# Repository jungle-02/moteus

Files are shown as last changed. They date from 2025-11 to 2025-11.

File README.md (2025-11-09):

# moteus brushless servo #

This contains full designs for the moteus brushless servo actuator,
including firmware and PCBs.

**WARNING**: This is not just a software project.  It includes designs
for moderately high power electronics.  It has not yet burned down my
(or anyone's that I know of) house, but there are no guarantees.

# Specifications #

| Name | r4.11 | c1 | n1 | x1 |
|---|---|---|---|---|
| Voltage Input | 10-44V | 10-51V | 10-54V | 10-54V |
| Peak Electrical Power  | 900W @ 30V | 250W @ 28V | 2kW @ 36V | 1.3kW @ 36V |
| Mass | 14.2g | 8.9g | 14.6g | 23.8g |
| Control Rate | 15-30kHz | - | - | - |
| PWM Switching Rate | 15-60kHz | - | - | - |
| CPU | STM32G4 | - | - | - |
| Uncooled phase current | 12A | 5A | 9A | 25A |
| Cooled phase current | 32A | 14A | 26A | 62A |
| Peak phase current | 100A | 20A | 100A | 120A |
| Communications | 5Mbps CAN-FD | - | - | - |
| Dimensions | 46x53mm | 38x38x9mm  | 46x46x8mm | 56x56x10mm  |

Assembled and tested boards can be purchased at: https://mjbots.com

# Directory structure #

* hw/ - hardware (mechanical and electrical designs)
  * controller/ - PCB design for moteus-r4.11
  * c1/ - PCB design for moteus-c1
  * n1/ - PCB design for moteus-n1
  * x1/ - PCB design for moteus-x1
* fw/ - firmware for brushless controller
* lib/ - client side software
* utils/ - diagnostic tools
* tools/ - bazel build configure
* docs/ - documentation

# Documentation #

* [Quick Start](https://mjbots.github.io/moteus/quick-start)
* [All Documentation](https://mjbots.github.io/moteus/)
* [Discord](https://discord.gg/W4hUpBb)

# Misc #

 * 

# How to support moteus development #

The easiest way to support development the moteus hardware and firmware is as follows:

1) Buy things from https://mjbots.com
2) Build awesome machines!

That's it!  If for some reason you want to go above and beyond, you can sponsor mjbots through github: https://github.com/sponsors/mjbots

# License #

All files contained in this repository, unless otherwise noted, are
available under an Apache 2.0 License:
https://www.apache.org/licenses/LICENSE-2.0

# Trademark #

mjbots Robotic Systems LLC owns and protects the "mjbots" and "moteus" trademarks in many jurisdictions.

If you want to use these names in your project or product, please read the [Trademark Policy](https://mjbots.com/trademark-policy)

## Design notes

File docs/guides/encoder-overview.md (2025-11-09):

# Encoder Overview

This section describes the various ways moteus can be configured to use encoders to sense the rotor, output, or auxiliary devices.  If you intend to only use the onboard on-axis magnetic encoder, you can skip this section.

## Introduction

moteus uses encoders to properly control a motor. Encoders provide the feedback needed to know where the motor is and how fast it's moving. Understanding which encoder(s) to use and how to configure them is one of the key decisions you need to make when designing a system, as for many applications encoder selection is the primary determinant of performance parameters like maximum stiffness, control stability and whether homing will be necessary.

Moteus uses encoders for two distinct purposes. First, it needs **commutation** feedback - the electrical relationship between the motor's stator and rotor to apply torque correctly. Second, it needs **output** feedback - the position and velocity of your output shaft to follow commanded trajectories. A single encoder can serve both purposes, or you can use separate encoders for each.

The good news is that moteus comes with an onboard AS5047P or MA600 magnetic encoder that works out of the box for many applications. This encoder mounts on-axis with the motor. For many use cases, especially those without gear reductions, this is all you need. However, if you're using hall sensors, need higher resolution, or have a gear reducer that you want to measure the output of a reducer or other auxiliary devices, you'll want to add other encoders.

In this guide, we'll cover a few common variants and leave the rest for [the detailed encoder reference](../reference/encoders.md).

## Common Configurations

Here are the most common encoder configurations you'll encounter:

**Default configuration (onboard encoder only):** The AS5047P or MA600 onboard encoder serves as both commutation and output sensor. This works well for many applications, especially those without a reducer installed or with a reducer where either the absolute position of the output is not required or a homing step is permitted.

**Adding hall sensors:** Hall effect sensors provide robust commutation feedback and are useful in high-vibration environments or when cost is a primary concern.  When used as the only encoder, the resulting system will have poor low-velocity and position tracking performance.

**Dual encoder setups:** Using one encoder for commutation (typically the onboard or hall sensors) and a separate high-resolution encoder for output position provides the best performance for precision applications.

These two options are described in separate guides below:

- [Motor with Hall Effects](hall-effects.md) - Adding hall sensors for commutation
- [Dual Encoders](dual-encoders.md) - Using separate encoders for commutation and output

Once again, for detailed information about encoder configuration parameters, see the [Detailed Encoder Reference](../reference/encoders.md).

## Next Steps

Once the encoder has been configured, then you are ready to move on to the [motor calibration procedure](calibration.md).

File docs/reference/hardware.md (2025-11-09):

# Hardware Specifications

## CAD and Models

| Name | 2D CAD | 3D Model |
|---|---|---|
| moteus-c1 |[2D CAD](https://github.com/mjbots/moteus/blob/0.1-20240430/hw/c1/r1.2/20240305-moteus-c1-r1_2.pdf) | [STEP](https://github.com/mjbots/moteus/blob/0.1-20240430/hw/c1/r1.2/20240305-moteus-c1-r1_2.step) |
| moteus-r4 |[2D CAD](https://github.com/mjbots/moteus/blob/main/hw/controller/r4.5/20210124-moteus-controller-r45-mechanical.pdf) | [STEP](https://github.com/mjbots/moteus/blob/main/hw/controller/r4.5/20210124-moteus-controller-r45-mechanical.step) |
| moteus-x1 | [2D CAD](https://drive.google.com/file/d/1R7wuc7vk1khD5ZvDWPy54Bx4PgHYiUCu/view) | [STEP](https://drive.google.com/file/d/19tJa4gzy0ZBWYYsaJA-Du0PgzoDWizjL/view?usp=sharing) |
| moteus-n1 | [2D CAD](https://drive.google.com/file/d/1Ic65vT8BSeTtqz6uqd8C7l68aOMy3bMz/view?usp=share_link) | [STEP](https://drive.google.com/file/d/1wxX5G6kX6M6YZGGSceiXTOUZycxRaSIE/view?usp=share_link) |

## Electrical Limits

| Name | Min Voltage | Nominal | Abs Max Voltage | Peak Output | 3V Aux |  5V Aux | 12V Aux |
|---|---|---|---|---|---|---|---|
| moteus-c1 | 10V | 24V | 51V (<= 12S) | 20A | 50mA | 100mA | N/A |
| moteus-r4 | 10V | 24V | 44V (<= 10S) | 100A | 100mA | N/A | N/A |
| moteus-x1 | 10V | 24V | 54V (<= 12S) | 120A | 100mA | 200mA | 150mA |
| moteus-n1 | 10V | 24V | 54V (<= 12S) | 100A | 100mA | 200mA | N/A |

## Power Limits

The allowable maximum power for each moteus controller depends upon
the input voltage and PWM switching frequency.  The below table gives
the maximum allowable power at `servo.pwm_rate_hz=30000`.

| Name | Peak power | | High input power |
|---|---|---|---|
| moteus-r4  | <= 30V 900W  | linear derated | >= 38V 400W |
| moteus-c1  | <= 28V 250W  | linear derated | >= 41V 150W |
| moteus-n1  | <= 36V 2000W | linear derated | >= 44V 1000W |

For other values of `servo.pwm_rate_hz`, the allowable maximum power
changes linearly with the PWM rate, so that at 15000, the maximum
power is half of that in the above table and at 60000 it is double
that.  Note however, that efficiency of the controller goes down
significantly at higher PWM rates.

The current power limit is reported in `servo_stats.max_power_W`.  The
controller will attempt to limit output phase current so as to stay
within this reported power limit in either direction, i.e. applying
power or regenerating energy.

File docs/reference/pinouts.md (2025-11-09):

# Pinouts

## moteus-c1



## moteus-r4



## moteus-x1



## moteus-n1



## Additional Information

### CAN Termination

CAN connections should be terminated by a 120 ohm resistor at both
ends of a bus.  Some mjbots products have built in termination
resistors, such as the pi3hat.  The mjcanfd-usb-1x and fdcanusb have a
software configurable termination resistor that is by default on.
moteus controllers have no termination resistors.  For very short
runs, the system will work terminated only on one side.  However, when
runs become longer than 0.5m, you will likely need to terminate both
ends.  This can be done by crimping a 120 ohm resistor into a JST PH3
connector and connecting it to the open data connector or by
purchasing a [CAN terminator](https://mjbots.com/products/jst-ph3-can-fd-terminator).

### Recommended Mating Hardware

| Connector | Mate P/N | Terminal P/N | Pre-crimped Wire |
|---|---|---|---|
| JST PH-3  | [PHR-3](https://mjbots.com/products/phr-3)  | [SPH-002T-P0.5L](https://mjbots.com/products/jst-ph-terminal) | [10cm, 30cm, 50cm PH3](https://mjbots.com/products/jst-ph3-cable) |
| JST GH-6  | [GHR-06V-S](https://mjbots.com/products/jst-gh6-housing) | [SSHL-002T-P0.2](https://www.digikey.com/en/products/detail/jst-sales-america-inc/SSHL-002T-P0-2/807828) | [28 AWG 20cm](https://mjbots.com/products/jst-gh-wire) |
| JST GH-7  | [GHR-07V-S](https://mjbots.com/products/jst-gh7-housing) | [SSHL-002T-P0.2](https://www.digikey.com/en/products/detail/jst-sales-america-inc/SSHL-002T-P0-2/807828) | [28 AWG 20cm](https://mjbots.com/products/jst-gh-wire) |
| JST GH-8  | [GHR-08V-S](https://mjbots.com/products/jst-gh8-housing) | [SSHL-002T-P0.2](https://www.digikey.com/en/products/detail/jst-sales-america-inc/SSHL-002T-P0-2/807828) | [28 AWG 20cm](https://mjbots.com/products/jst-gh-wire) |
| JST ZH-4  | [ZHR-4](https://www.digikey.com/en/products/detail/jst-sales-america-inc/ZHR-4/608643) | [SZH-002T-P0.5](https://www.digikey.com/en/products/detail/jst-sales-america-inc/SZH-002T-P0-5/527363) | |
| JST ZH-6  | [ZHR-6](https://www.digikey.com/en/products/detail/jst-sales-america-inc/ZHR-6/527361) | [SZH-002T-P0.5](https://www.digikey.com/en/products/detail/jst-sales-america-inc/SZH-002T-P0-5/527363) | [stm32 programmer](https://mjbots.com/products/stm32-programmer) |
| AMass XT30 | [XT30U-F](https://mjbots.com/products/xt30u-f) | | |

### Recommended Low Cost Manual Crimp Tools

- **JST PH**: [TU-190-08](https://www.amazon.com/TU-190-08-Terminals-Tool-Crimping-0-08-0-5sq-mm/dp/B01M25OLZY)
- **JST ZH**: [PEBA 1020M](https://www.amazon.com/PEBA-Ratcheting-Connectors-Crimping-terminals/dp/B0D7PKLBZT)
- **JST GH**: [PEBA 1020M](https://www.amazon.com/PEBA-Ratcheting-Connectors-Crimping-terminals/dp/B0D7PKLBZT)

### moteus-r4 - Pico-SPOX 6 ENC

The ENC/AUX1 connector on moteus-r4 are intended to be populated with
a Molex Pico-SPOX 6 connector PN 0874380643, or as an alternate, TE
5-1775444-6.

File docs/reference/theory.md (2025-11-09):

# Theory of Operation

The moteus controller is intended to drive 3 phase brushless motors
using field oriented control.  It has an integrated magnetic encoder
for sensing the rotor position, 3 half-H bridges for switching power
to each of the three phases, and current sense capability on each of
the three phases.

The primary control mode, labeled as "position" mode in the rest of
this document is a two stage cascaded controller, with both running at
the switching frequency (by default 30kHz).

The outermost stage is an optional limited acceleration and velocity
trajectory planner.  Within that is an integrated position/velocity
PID controller with optional feedforward torque.  The output of that
loop is a desired torque/current for the Q phase of the FOC
controller.

The inner stage is a current mode PI controller.  Its output is the
desired voltage value for the Q phase.  Then the magnetic encoder is
used to map the D/Q phase voltage values to the 3 phases of the motor.

Control Structure

More precisely, the "Position Controller" implements the following
control law:

```
acceleration = trajectory_follower(command_position, command_velocity)
control_velocity = command_velocity OR control_velocity + acceleration * dt OR 0.0
control_position = command_position OR control_position + control_velocity * dt
position_error = control_position - feedback_position
velocity_error = control_velocity - feedback_velocity
position_integrator = limit(position_integrator + ki * position_error * dt, ilimit)
torque = position_integrator +
         kp * kp_scale * position_error +
         kd * kd_scale * velocity_error +
         command_torque
```

And the "Current Controller" implements the following control law:

```
current_error = command_current - feedback_current
current_integrator = limit(current_integrator + ki * current_error, ilimit)
voltage = current_integrator + kp * current_error
```

Since PID scaling for the position mode loop can be adjusted on a
cycle-by-cycle basis with the `kp_scale` and `kd_scale` terms, this
allows you to operate the controller with full
position/velocity/torque control, or velocity/torque, or just torque,
or any combination seamlessly throughout the control cycle.

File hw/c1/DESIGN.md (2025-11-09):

moteus-c1 is a small form factor controller with the flexibility of
the moteus-n1, but designed for lower power and current applications.

# r1.1 fixes #

 * U2 3.3V regulator has enable pin undriven
 * Switched U2 to part TLV70233PDBVR which is SOT23-5 and has better
   thermal properties
 * removed gate drive resistors and discharge diodes
 * moved C7 away from AUX1/AUX2 pins
 * switch can terminator (R6) to 0603 and move further away from power
   pad
 * rev silk version to r1.1
 * version divider pulled low
 * revved TVS to the 48V version, so 3V lower than before... that will
   make the rated max voltage be 51V instead of 54V
 * added unpopulated resistor and capacitor between power ground and a
   mounting hole

# TODO #

# r1.0 ERRATA #
 * C7 blocks access to the through hole pins (they barely fit, but
   could use a bit more margin)
 * can termination resistor pad is too close to power pin of XT30
 * high side FET trace to DRV is too small compared to gate drive
   trace and should be swapped around to be a pair with gate drive
 * board version divider should never be floating, needs to be
   pulled low for next rev
 * remove gate drive resistors and reverse diodes
 * 3.3V regulator should be the SOT-23 package that has better
   thermals
 * need to fully lay out what the family pullup/pulldowns are so
   that I can be sure they can all be distinguished

r1.1 MAYBE
 * possible remove all the gate drive resistors and protection diodes?
 * maybe lower max voltage to 51V and drop the TVS diode by one step

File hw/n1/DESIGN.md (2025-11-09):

moteus-n1 is intended as a higher power/voltage, more flexible, yet
smaller in footprint version of the moteus brushless controller.

# Features #

 * 51V max voltage (vs 44V for moteus)
 * More flexible aux1/aux2 connectors
   * both JST GH (aux1 is 8 pin, aux2 is 7 pin)
   * 200mA of 5V between both connectors
   * 200mA of 3V between both connectors
   * aux1 now has two pins that can be used even if onboard encoder is used
   * SPI on both connectors
   * UART on both connectors
   * ADC on both connectors
   * Sine/cosine on both connectors
   * Hardware quadrature (higher count rates)
 * RS422 transceiver and connector (consumes the two spare pins on AUX1)
 * No connectors required on bottom of board for smaller footprint
 * Optional solder pads for power in for higher current capability
 * Variants
   * optional power/CAN connectors on bottom for daisy chaining
 * CAN transceiver with 58V bus fault voltage
 * 46x46mm

# Pin Allocation #

 * PA0  - MOTOR 1       (fast ADC1/2)
 * PA1  - MOTOR 2       (fast ADC1/2)
 * PA2  - MOTOR 3       (fast ADC1)
 * PA3  - CURRENT       (fast ADC1)
 * PA4  - DEBUG_DAC
 * PA5  - AUX1_A
 * PA6  - CURRENT       (fast ADC2)
 * PA7  - AUX1_C
 * PA8  - TSENSE2       (fast ADC5)
 * PA9  - VSENSE        (fast ADC5)
 * PA10 - AUX2_A
 * PA11 - AUX2_B
 * PA12 - AUX2_I2C_PULLUP
 * PA13 - SWDIO
 * PA14 - SWCLK
 * PA15 - AUX1_D
 * PB0  - DRV8353 CS
 * PB1  - CURRENT        (fast ADC3)
 * PB2  - AS5047P CS     (ADC2)
 * PB3  - AUX1_E
 * PB4  - AUX1_B
 * PB5  - FDCAN2_RX
 * PB6  - FDCAN2_TX
 * PB7  - AUX2_C
 * PB8  - AUX1_I2C_PULLUP
 * PB9  - AUX1_E
 * PB10 - RS422_RE
 * PB11 - RS422_DE      (ADC1/2)
 * PB12 - TSENSE1      (fast ADC4)
 * PB13 - MOTOR_FAULT  (fast ADC3)
 * PB14 - AUX1_A       (fast ADC1/4)
 * PB15 - LED1         (fast ADC4)
 * PC4  - AUX2_B       (fast ADC2)
 * PC6  - LED2
 * PC10 - DRV8323 SCK
 * PC11 - DRV8323 MISO
 * PC13 - DRV8323 MOSI
 * PC14 - MOTOR_ENABLE
 * PC15 - MOTOR_HIZ
 * PF0 - AUX2_A
 * PF1 - AUX2_D

# Pins Required #

     * LEDs - 2
     * as5047 CS - 1
     * drv8353 CS - 1
     * 2x temp sense - 2
     * debug uart - 2
     * swd - 2
     * DAC debug?
     * voltage sense - 1
     * aux ADC - 2
     * primary aux - 1
     * CAN - 2
     * current sense - 3
       * needs to be "fast" ADC channels
     * aux fixed conn - 2
     * primary fixed conn - 4 (SPI shared with as5047)
     * drv8353 SPI - 3
     * gate PWM - 3

# Connectors #

## Aux 1 ##

 * notional pins (8  pins)
  * 5V
  * 3.3v
  * A: SPI1_SCK  / ADC1 / TIM2_CH1                             - PA5 / PB14
  * B: SPI1_MISO /      / TIM3_CH1 /          / USART2_RX / 5V - PB4
  * C: SPI1_MOSI / ADC2 / TIM3_CH2                             - PA7
  * D:           /      / TIM2_CH1 / I2C1_SCL / USART2_RX / 5V - PA15
  * E: SPI1_SCK  /      / TIM2_CH2 / I2C1_SDA / USART2_TX / 5V - PB3 / PB9
  * gnd

## Aux 2 ##

 * 3V and 5V power
 * I2C
 * quadrature
 * index
 * uart
 * SPI
 * PA14/PA15 have I2C1 and USART2 and TIM8_CH1/2
 * PB8/PB9 have I2C1 and USART3 and TIM4_CH3/4
 * TIM1/2 options: PA0/1/2/3/5/6/7/12/15
                   PB2/3/4/5/6/7/8/9/14/15
 * notional pins (7 pins)
   * 5V
   * 3V
   * A: SPI2 SCK  /           /          / ADC2 /           - PF1
   * B: SPI2 MISO / USART1_RX / I2C2_SDA / ADC1             - PA10 / PF0
   * C: SPI2 MOSI / USART1_TX / I2C2_SCL / ADC2 / TIM4_CH1  - PA11 / PC4
   * D:             USART1_RX /                 / TIM4_CH2  - PB7
   * gnd

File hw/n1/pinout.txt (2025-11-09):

PA0 TIM2_CH1 TIM5_CH1 ADC1_IN1 ADC2_IN1 ANALOG
PA1 TIM2_CH2 TIM5_CH2 ADC1_IN1 ADC2_IN1 ANALOG
PA2 5V USART2_TX LPUART1_TX ADC1_IN3 ANALOG
PA3 USART2_RX LPUART1_RX ADC1_IN4 ANALOG
PA4 TIM3_CH2 ADC2_IN17 ANALOG
PA5 TIM2_CH1 SPI1_SCK ADC2_IN13 ANALOG
PA6 TIM3_CH1 SPI1_MISO ADC2_IN3 ANALOG
PA7 TIM3_CH2 SPI1_MOSI ADC2_IN4 ANALOG
PA8 5V I2C3_SCL I2C2_SDA TIM1_CH1 ADC5_IN1 ANALOG
PA9 5V I2C2_SCL TIM1_CH2 USART1_TX ADC5_IN2 ANALOG
PA10 5V SPI2_MISO USART1_RX ANALOG
PA11 5V SPI2_MOSI TIM4_CH1
PA12 5V TIM4_CH2
PA15 5V TIM2_CH1 TIM8_CH1 I2C1_SCL USART2_RX
PB0 ADC3_IN12 ADC1_IN15 ANALOG
PB1 ADC3_IN1 ADC1_IN12 ANALOG
PB2 TIM5_CH1 TIM20_CH1 ADC2_IN12 ANALOG
PB3 5V TIM2_CH2 SPI1_SCK SPI3_SCK USART2_TX
PB4 5V TIM3_CH1 SPI1_MISO SPI3_MISO USART2_RX
PB5 5V TIM3_CH2 I2C1_SMBA SPI1_MOSI SPI3_MOSI I2C3_SDA
PB6 5V TIM4_CH1 TIM8_CH1 USART1_TX
PB7 5V TIM4_CH2 I2C4_SDA I2C1_SDA USART1_RX LPTIM1_IN2
PB8 5V I2C_SCL USART3_RX TIM8_CH2
PB9 5V I2C1_SDA USART3_TX
PB10 USART3_TX LPUART1_RX OPAMP3_VINM OPAMP4_VINM ANALOG
PB11 USART3_RX LPUART1_TX ADC1_IN14 ADC2_IN14 OPAMP4_VINP ANALOG
PB12 ADC4_IN13 ADC1_IN11 OPAMP6_VINP ANALOG
PB13 SPI2_SCK ADC3_IN5 OPAMP3_VINP OPAMP4_VINP OPAMP5_VINP ANALOG
PB14 TIM15_CH1 SPI2_MISO ADC4_IN4 ADC1_IN5 OPAMP2_VINP OPAMP5_VINP ANALOG
PB15 SPI2_MOSI ADC4_IN5 ADC2_IN15 OPAMP5_VINM ANALOG
PC4 5V I2C2_SCL USART1_TX ADC2_IN5 ANALOG
PC5 USART1_RX ADC2_IN11 ANALOG
PC6 5V TIM3_CH1 TIM8_CH1 I2C4_SCL
PC10 5V UART4_TX SPI3_SCK USART3_TX
PC11 5V UART4_RX SPI3_MISO USART3_RX I2C3_SDA
PC13 5V TIM5_CH2 UART5_TX SPI3_MOSI
PF0 5V I2C2_SDA ADC1_IN10 ANALOG
PF1 5V SPI2_SCK ADC2_IN10 ANALOG

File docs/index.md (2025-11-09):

# moteus Brushless Servo Documentation

Welcome to the documentation site for the moteus brushless motor controller.

## What is moteus?

moteus controllers are high-performance modular brushless motor controllers with integrated on-axis magnetic encoders, designed for robotics applications. They feature:

- **Field Oriented Control (FOC)** for 3-phase brushless motors
- **Integrated magnetic encoder** for precise position sensing
- **High-speed CAN-FD communication** at 5Mbps
- **Multiple control modes**: Position, velocity, and torque control with acceleration and velocity limited trajectories
- **Fast control loops** running at 15-30kHz

## Hardware Variants

| Name | Voltage Input | Peak Power | Mass  | Dimensions |
|---|---|---|---|---|
| r4.11  | 10-44V | 900W @ 30V | 14.2g | 46x53mm |
| c1 | 10-51V | 250W @ 28V | 8.9g  | 38x38x9mm |
| n1 | 10-54V | 2kW @ 36V | 14.6g | 46x46x8mm |
| x1 | 10-54V | 1.3kW @ 36V | 23.8g | 56x56x10mm |

Assembled and tested boards can be purchased at [mjbots.com](https://mjbots.com)

## Documentation

- [Quick Start](quick-start.md)
- [Using Moteus](guides/mechanical-setup.md)
- [Integration](integration/python.md)
- [Troubleshooting](troubleshooting/calibration.md)
- [Reference](reference/pinouts.md)

## Community & Support

- [Discord Community](https://discord.gg/W4hUpBb)
- [GitHub Repository](https://github.com/mjbots/moteus)
- [Purchase Hardware](https://mjbots.com)

## License

All files in this repository are available under the [Apache 2.0 License](https://www.apache.org/licenses/LICENSE-2.0).

!!! note "Trademark Notice"
    mjbots Robotic Systems LLC owns and protects the "mjbots" and "moteus" trademarks. Please read the [Trademark Policy](https://mjbots.com/trademark-policy) if you want to use these names in your project.

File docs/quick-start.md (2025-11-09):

# Quick Start Guide

New to moteus?  Work through these sections in order.  The first set
is if you have a bare board, the second is if you are starting from a
developer kit.

## Setup Overview for Bare Boards

If you have a bare moteus board and a motor, these steps are for you.

1. **[Mechanical Setup](guides/mechanical-setup.md)** - Mount the encoder magnet and controller
2. **[Electrical Setup](guides/electrical-setup.md)** - Connect phase wires and power
3. **[Software Installation](guides/software-installation.md)** - Install and run tview
4. **[Configuration](guides/configuration.md)** - Set essential parameters
5. **[Encoder Overview](guides/encoder-overview.md)** - Understand encoder options (if using external encoders)
6. **[Calibration](guides/calibration.md)** - Calibrate the controller for your motor
7. **[PID Tuning](guides/pid-tuning.md)** - Tune the position control constants
8. **[Control Modes](guides/control-modes.md)** - Learn how to control the motor

## Developer Kit Users

If you're starting from a developer kit, the motor is already mounted,
configured, calibrated and tuned. Your job is easier, yay!  Just follow these steps:

1. **[Software Installation](guides/software-installation.md)** - Install tview
2. **[Control Modes](guides/control-modes.md)** - Start controlling your motor

## Need Help?

- **[Troubleshooting](troubleshooting/calibration.md)** - Common issues and solutions
- **[Discord Community](https://discord.gg/W4hUpBb)** - Get help from the community
- **[GitHub Issues](https://github.com/mjbots/moteus/issues)** - Report bugs or request features
- **[info@mjbots.com](mailto:info@mjbots.com)** - Email support

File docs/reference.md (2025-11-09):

# Reference Documentation

This page has been reorganized. Please use the navigation menu or the links below to find the content you're looking for.

## Quick Links

### Theory and Operation

**[Theory of Operation](https://mjbots.github.io/moteus/reference/theory/)** - Controller architecture and control laws

**[Usage Modes / Control Modes](https://mjbots.github.io/moteus/guides/control-modes/)** - Position, velocity, and torque control modes

### Configuration

**[Initial Parameters / Configuration](https://mjbots.github.io/moteus/guides/configuration/)** - Getting started with configuration

**[Encoder Configuration](https://mjbots.github.io/moteus/guides/encoder-overview/)** - Encoder setup and configuration

**[Auxiliary Port](https://mjbots.github.io/moteus/reference/encoders/#auxiliary-port)** - Auxiliary connector configuration and pinouts

**[AUX1/ENC Pins](https://mjbots.github.io/moteus/reference/encoders/#r411-pins-aux1enc)** - r4.11 AUX1/ENC connector pinout

**[AUX2/ABS Pins](https://mjbots.github.io/moteus/reference/encoders/#r411-pins-aux2abs)** - r4.11 AUX2/ABS connector pinout

**[AUX GPIO Output Control](https://mjbots.github.io/moteus/protocol/diagnostic/#aux1-out-set-gpio-output-values)** - Setting GPIO outputs via diagnostic commands

**[AUX UART Mode](https://mjbots.github.io/moteus/reference/encoders/#uart)** - Configuring UART on auxiliary ports

**[Pin Capabilities](https://mjbots.github.io/moteus/reference/encoders/#io-pin-capabilities)** - Available pin modes and configurations

### Configuration Parameters

**[id.id](https://mjbots.github.io/moteus/reference/configuration/#idid)** - Device ID configuration

**[servo.default_timeout_s](https://mjbots.github.io/moteus/reference/configuration/#servodefault_timeout_s)** - Command timeout configuration

**[servo.flux_brake_margin_voltage](https://mjbots.github.io/moteus/reference/configuration/#servoflux_brake_margin_voltage)** - Flux braking voltage threshold

**[servo.max_power_W](https://mjbots.github.io/moteus/reference/configuration/#servomax_power_w)** - Maximum power limit

**[servo.pid_position](https://mjbots.github.io/moteus/reference/configuration/#servopid_position)** - Position PID controller parameters

**[servopos.position_min](https://mjbots.github.io/moteus/reference/configuration/#servoposposition_min)** - Minimum position limit

**[motor_position.output.offset/sign](https://mjbots.github.io/moteus/reference/configuration/#motor_positionoutputoffsetsign)** - Output encoder offset and sign

**[motor_position.rotor_to_output_ratio](https://mjbots.github.io/moteus/reference/configuration/#motor_positionrotor_to_output_ratio)** - Gear reduction ratio

**[Configuration Commands](https://mjbots.github.io/moteus/protocol/diagnostic/#conf-configuration)** - Reading and writing configuration via console

### Register Reference

**[0x000 - Mode](https://mjbots.github.io/moteus/protocol/registers/#0x000-mode)** - Operational mode register

**[0x00f - Fault Code](https://mjbots.github.io/moteus/protocol/registers/#0x00f-fault-code)** - Fault status register

**[0x014/0x15/0x16 - Voltage Phase A/B/C](https://mjbots.github.io/moteus/protocol/registers/#0x014-0x15-0x16-voltage-phase-a-b-c)** - Phase voltage control registers

**[0x020 - Position Command](https://mjbots.github.io/moteus/protocol/registers/#0x020-position-command)** - Position setpoint register

**[0x021 - Velocity Command](https://mjbots.github.io/moteus/protocol/registers/#0x021-velocity-command)** - Velocity setpoint register

**[0x023 - Kp Scale](https://mjbots.github.io/moteus/protocol/registers/#0x023-kp-scale)** - Proportional gain scaling

**[0x025 - Maximum Torque](https://mjbots.github.io/moteus/protocol/registers/#0x025-maximum-torque)** - Torque limit register

**[0x028 - Velocity Limit](https://mjbots.github.io/moteus/protocol/registers/#0x028-velocity-limit)** - Trajectory velocity limit

**[0x058 - Encoder Validity](https://mjbots.github.io/moteus/protocol/registers/#0x058-encoder-validity)** - Encoder status bitfield

**[0x05c - Aux1 GPIO Command](https://mjbots.github.io/moteus/protocol/registers/#0x05c-aux1-gpio-command)** - GPIO output control register

**[0x070 - Millisecond Counter](https://mjbots.github.io/moteus/protocol/registers/#0x070-millisecond-counter)** - System timestamp register

**[0x131 - Set Output Exact](https://mjbots.github.io/moteus/protocol/registers/#0x131-set-output-exact)** - Force absolute position register

**[0x150-0x153 - UUID](https://mjbots.github.io/moteus/protocol/registers/#0x150-0x153-uuid)** - Device UUID registers

**[0x154-0x157 - UUID Mask](https://mjbots.github.io/moteus/protocol/registers/#0x154-0x157-uuid-mask)** - UUID filtering registers

**[Register Mappings](https://mjbots.github.io/moteus/protocol/registers/#mappings)** - Data type encodings and scaling

**[Register List](https://mjbots.github.io/moteus/protocol/registers/#registers)** - Complete register documentation

### CAN Protocol

**[CAN Format](https://mjbots.github.io/moteus/protocol/can/#can-format)** - CAN-FD frame structure

**[Write Registers](https://mjbots.github.io/moteus/protocol/can/#write-registers)** - Register write subframe format

**[CAN Protocol Example](https://mjbots.github.io/moteus/protocol/can/#example)** - Sample CAN frame breakdown

**[Sending Multiple Commands](https://mjbots.github.io/moteus/reference/client-tools/#sending-multiple-commands-at-once)** - Batching commands in tview

**[Communicating with Specific Device](https://mjbots.github.io/moteus/reference/client-tools/#communicating-with-a-specific-device)** - Targeting devices by ID

**[CAN Bit Timings](https://mjbots.github.io/moteus/platforms/socketcan/#bit-timings)** - socketcan bitrate configuration

**[Clock-Specific Bit Timings](https://mjbots.github.io/moteus/platforms/socketcan/#bit-timings)** - 40MHz and 80MHz configurations

### Diagnostic Commands

**[Diagnostic Protocol](https://mjbots.github.io/moteus/protocol/diagnostic/)** - Console command reference

**[d pwm](https://mjbots.github.io/moteus/protocol/diagnostic/#d-pwm)** - Raw PWM control command

**[d nearest](https://mjbots.github.io/moteus/protocol/diagnostic/#d-nearest)** - Set output nearest command

**[d cfg-set-output](https://mjbots.github.io/moteus/protocol/diagnostic/#d-cfg-set-output)** - Configure output encoder

### Hardware Reference

**[Pinouts](https://mjbots.github.io/moteus/reference/pinouts/)** - Connector pinouts for all board variants

**[Debug Port (JST ZH-6)](https://mjbots.github.io/moteus/reference/pinouts/)** - SWD debug connector

**[n1/c1 AUX2 (JST GH-7)](https://mjbots.github.io/moteus/reference/pinouts/)** - n1 and c1 auxiliary port connector

**[r4 ABS (JST ZH-4)](https://mjbots.github.io/moteus/reference/pinouts/)** - r4 absolute encoder connector

**[r4 ENC (Pico-SPOX-6)](https://mjbots.github.io/moteus/reference/pinouts/)** - r4 incremental encoder connector

**[Hardware Specifications](https://mjbots.github.io/moteus/reference/hardware/)** - Electrical ratings and mechanical information

**[Application Limits](https://mjbots.github.io/moteus/reference/limits/)** - Position, velocity, and performance constraints

### Calibration and Tuning

**[Calibration](https://mjbots.github.io/moteus/guides/calibration/)** - Motor and encoder calibration procedures

**[PID Tuning](https://mjbots.github.io/moteus/guides/pid-tuning/)** - Controller tuning methodology

### Firmware and Tools

**[Flashing and Building Firmware](https://mjbots.github.io/moteus/reference/firmware/)** - Firmware compilation and installation

**[tview Usage](https://mjbots.github.io/moteus/reference/client-tools/#tview-usage)** - Command-line tool documentation

### Deployment

**[Deployment Considerations](https://mjbots.github.io/moteus/guides/electrical-setup/)** - Production design guidelines and safety considerations

### Additional Topics

**[Hall Effect Sensors](https://mjbots.github.io/moteus/reference/encoders/#hall-sensor)** - Using motors with hall effect sensors or configuring hall sensor pins

**[Position Mode](https://mjbots.github.io/moteus/guides/control-modes/#understanding-position-mode)** - Position control details

**[Torque Control](https://mjbots.github.io/moteus/guides/control-modes/#torque-control)** - Direct torque control mode

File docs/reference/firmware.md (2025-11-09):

# Flashing and building firmware

moteus controllers have both upgradeable firmware and a permissively licensed source code for the firmware.  This section describes how to flash new (or old) versions of the firmware, and how to build it from source.

## Flashing over CAN

The latest firmware can be downloaded from: [https://github.com/mjbots/moteus/releases](https://github.com/mjbots/moteus/releases)

You need the file named YYYYMMDD-moteus-HASH.elf NOT the one named
"bootloader".

Download that file and save it somewhere on your computer, then
substitute its path in place of `path/to/file.elf` in the following
command.

```
python3 -m moteus.moteus_tool --target 1 --flash path/to/file.elf
```

## Building firmware

To build the moteus firmware, an x86-64 Ubuntu 20.04, 22.04, or 24.04
system is required.

```
tools/bazel build --config=target //:target
```

## Flash from the SWD port

If CAN-FD is inoperative, then new firmware can be flashed using the SWD connector on each moteus.  First install dependencies:

```
sudo apt install openocd binutils-arm-none-eabi
```

Then attach a [stm32 programmer](https://mjbots.com/products/stm32-programmer) to the USB port on your computer and the SWD port on the moteus.

The firmware can be built and flashed using:

```
tools/bazel build --config=target //fw:flash
```

Or, if already built, flashed using:

```
./fw/flash.py
```

The python script can be used to flash pre-compiled images as well:

```
./fw/flash.py path/to/firmware.elf path/to/bootloader.elf
```

## Debug from the SWD port

gdb can be used for debugging the firmware when an [stm32 programmer](https://mjbots.com/products/stm32-programmer) is attached to the SWD port.  First, install dependencies:

```
sudo apt install gdb-multiarch
```

Then, in one terminal run:

```
./run_openocd_noreset.sh
```

In another terminal run:

```
gdb-multiarch -x moteus-debug.gdb bazel-out/stm32g4-opt/bin/moteus.elf
```

Debugging hints:

- **Flashing Red Light**: This means a debug assertion failed.  Using `bt` to get a backtrace will tell you the call site.
- **Pool Size**: The firmware allocates data from a fixed size pool during initialization.  If new structures are added, this size can be exceeded.  Either reduce the size of structures, or increase the size of the pool.
- **Optimizations**: The moteus firmware must have optimizations enabled globally.  This makes debugging challenging.  Some strategies:
 - Expose data you need to structures available to tview
 - Single step through assembly
 - Use the `__attribute__((optimize("O0")))` on individual functions to disable optimization

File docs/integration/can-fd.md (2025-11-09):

# CAN-FD

The python and C++ libraries are not required to command and monitor moteus, they just make it easier.  Any system capable of generating and receiving CAN-FD frames with the appropriate timing can be used.  Here are some hints to make that easier.

## Bit timing and basic communication

Moteus requires 1Mbps/5Mbps CAN-FD timing, a sample point of 0.666, and works best if the SJW and DSJW settings are as large as possible.

If communication is not working, it is recommended to attach a mjcanfd-usb-1x to the bus at the same time as your host and use it to capture frames.  Any serial application (or `cat` on Linux) can be used to read the output.  Since they start with the same timings as moteus, you can use that to identify if your frames are being received and being responded to.

## Decoding frames observed on the bus

There exists a tool in the moteus repository to decode CAN-FD frames sent to or from moteus that can be invaluable in diagnosing what you are sending and why moteus is or is not responding to it.  First, capture a hex formatted dump of the CAN-FD frame in question.  Then:

```
moteus$ ./utils/decode_can_frame.py 1100110F
11 - READ_REGISTERS - INT8 1 registers
  00 - Starting at reg 0x000(MODE)
11 - READ_REGISTERS - INT8 1 registers
  0f - Starting at reg 0x00f(FAULT)
```

and the corresponding response:

```
moteus$ ./utils/decode_can_frame.py 210000210F00
21 - REPLY - 0 1 registers
  00 - Starting at reg 0x000(MODE)
   00 - Reg 0x000(MODE) = 0(STOPPED)
21 - REPLY - 0 1 registers
  0f - Starting at reg 0x00f(FAULT)
   00 - Reg 0x00f(FAULT) = 0
```

## Generating appropriate command frames

The [CAN-FD reference](../protocol/can.md) and [register reference](../protocol/registers.md) contains the information necessary to generate and parse frames.  However, it can be a lot to digest.  You can use the [python library](../integration/python.md) to quickly get example frames that accomplish a given task.  First, create a python script that accomplishes what you want.  Then, in an interactive python REPL:

```
>>> print(c.make_position(position=1, velocity=2, query=True).data.hex())
01000a0e200000803f0000004011001f01130d
```

Where the arguments to `make_position` correspond to the action you want to accomplish.  You can verify the contents of this frame using `decode_can_frame.py`:

```
moteus$ ./utils/decode_can_frame.py 01000a0e200000803f0000004011001f01130d
01 - WRITE_REGISTERS - 0 1 registers
  00 - Starting at reg 0x000(MODE)
   0a - Reg 0x000(MODE) = 10(POSITION)
0e - WRITE_REGISTERS - 3 2 registers
  20 - Starting at reg 0x020(COMMAND_POSITION)
   0000803f - Reg 0x020(COMMAND_POSITION) = 1.0
   00000040 - Reg 0x021(COMMAND_VELOCITY) = 2.0
11 - READ_REGISTERS - INT8 1 registers
  00 - Starting at reg 0x000(MODE)
1f - READ_REGISTERS - F32 3 registers
  01 - Starting at reg 0x001(POSITION)
13 - READ_REGISTERS - INT8 3 registers
  0d - Starting at reg 0x00d(VOLTAGE)
```

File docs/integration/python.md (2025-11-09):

# Python Client Library

moteus provides a python library that can be used to command and control moteus controllers using a supported CAN-FD adapter.

## Installation

To install, just use:

```
pip install moteus
```

Or add to your `requirements.txt` file, or via whatever mechanism your project uses.

## Basic Usage

There are two basic approaches to using the python library.  The first is the easiest, although does not provide optimal bus utilization if that is a design requirement.

First, construct one or more controller instances:

```python
import asyncio
import moteus

async def main():
    c1 = moteus.Controller(id=1)
    c2 = moteus.Controller(id=2)
    # ...

if __name__ == '__main__':
    asyncio.run(main())
```

Then, at regular intervals, send commands to each of the devices using the `set_` variant of each API.

```python
while True:
  c1_result = await c1.set_position(
      position=math.nan, velocity=1.0, accel_limit=0.5, query=True)
  c2_result = await c2.set_position(
      position=math.nan, velocity=0.5, accel_limit=0.25, query=True)

  c1_position = c1_result.values[moteus.Register.POSITION]
  c2_position = c2_result.values[moteus.Register.POSITION]

  print(c1_position, c2_position)

  await asyncio.sleep(0.01)
```

## `.cycle` based usage

If bus utilization or a high update rate is desired, an alternate API can be used to maximize performance.  In this API, the commands are constructed in advance using `make_` variants of commands, then submitted to the library in a group.

```python
import argparse
import asyncio
import moteus

async def main():
    parser = argparse.ArgumentParser()
    moteus.make_transport_args(parser)
    args = parser.parse_args()

    transport = moteus.get_singleton_transport(args)
    c1 = moteus.Controller(id=1, transport=transport)
    c2 = moteus.Controller(id=2, transport=transport)
    # ...

    while True:
        results = await transport.cycle([
           c1.make_position(position=math.nan, query=True)
           c2.make_position(position=math.nan, query=True),
           ])

        # Print the ID and position of all received responses.
        print(", ".join(
            f"{x.source} " +
            f"{x.values[moteus.Register.POSITION]}"
            for x in results))

        await asyncio.sleep(0.01)

if __name__ == '__main__':
    asyncio.run(main())
```

## Querying alternate registers

By default, only a limited set of registers are queried.  The full set of available registers can be found in the [register reference documentation](../protocol/registers.md).  The easiest way to query additional registers is to pass an alternate `QueryResolution` structure to the `Controller` constructor.

```python
qr = moteus.QueryResolution()
qr.power = moteus.F32
c = moteus.Controller(id=1, query_resolution=qr)
```

If the register you want is not available in the `QueryResolution` structure, it can be requested using the `_extra` method:

```python
qr = moteus.QueryResolution()
qr._extra = {
    moteus.Register.ENCODER_1_POSITION: moteus.F32,
    moteus.Register.ENCODER_1_VELOCITY: moteus.F32,
}
c = moteus.Controller(id=1, query_resolution=qr)
```

## API Reference

- [Python API Reference](../reference/python.md)

## Related Sections

- [Control Modes](../guides/control-modes.md) - Understanding different control strategies
- [Configuration Parameters](../reference/configuration.md) - Available parameters
- [Raspberry Pi Setup](../platforms/raspberry-pi.md) - Platform-specific configuration

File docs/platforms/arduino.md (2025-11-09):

# Arduino

moteus provides a simplified version of the C++ library for use with Arduino compatible microcontroller systems.

## Installation

Open the Arduino library manager, search for "moteus" and install.  Then open one of the examples and modify it.  "WaitComplete" is a good one to get started with.

## Supported hardware ##

**Microcontroller**: Nearly any board compatible with the Arduino software is supported

**CAN-FD**: The library only supports CAN-FD controllers and transceivers compatible with the [acan2517FD library](https://github.com/pierremolinaro/acan2517fd).

There are two pieces of configuration that are board and controller specific.

### Pin Assignments ###

The `ACAN2517FD` constructor requires that it be passed the correct pins that are used for the SPI peripheral connected to the MCP2517FD controller.  For an external controller, you can use the pins you have physically wired to the controller.  For an integrated MCP2517FD you will need to look at your board documentation.

```cpp
#define MCP2517_CS  17
#define MCP2517_INT 7
// For the Longan CANBed FD, the "SPI" peripheral determines which
// pins are used.
ACAN2517FD can(MCP2517_CS, SPI, MCP2517_INT);
```

### CAN-FD Timing ###

You need to match the CAN-FD base clock rate that your adapter uses.  Different adapters have different base clock rates.

**Longan Labs CANBed FD**: This board uses a 20MHz clock

**Mikro MCP2517FD Click**: This board defaults to a 40MHz clock, but can be configured by jumper.

Regardless, you need to pass the correct clock rate using the `ACAN2517FDSettings` object.

```cpp
ACAN2517FDSettings settings(
    ACAN2517FDSettings::OSC_20MHz,
    1000ll * 1000ll,
    DataBitRateFactor::x1);

settings.mArbitrationSJW = 2;
settings.mDriverTransmitFIFOSize = 1;
settings.mDriverReceiveFIFOSize = 2;

const uint32_t errorCode = can.begin(settings, [] { can.isr(); });
```

## Caveats

There are some caveats when controlling moteus from a microcontroller.

### CAN-FD adapter still required

While you can command and control moteus from the Arduino library, there is currently no mechanism to calibrate a new motor with a controller.  Thus you *must* have a CAN-FD adapter that is able to be connected to a computer with an operating system in order to run the [calibration process](../guides/calibration.md) and it is also much easier to use one to set the configuration and tune the PID gains.

### Teensy 4 integrated CAN-FD controller is *not* supported

There exists an unsupported PR to handle this, but at the moment, the CAN-FD controller integrated into Teensy 4 microcontrollers is not supported by the Arduino library.  External MCP2517FD controllers work just fine with any Teensy controller.

### Termination

Many external MCP2517FD controller/transceivers do not have termination resistors.  To operate correctly, a CAN-FD bus is intended to have 2 120ohm resistors between CANL and CANH, one at each end of the bus.  Often short busses will work acceptly with only 1 termination resistor, but never with 0.

### Flash and storage limitations

With some smaller Arduino platforms, notably the Arduino Uno or Longan Labs CANBed FD, the combination of the ACAN2517FD library and the moteus library can consume a significant fraction of the flash and RAM available. For simple applications this isn’t a problem, but if you want to execute something more complex, you may be better served using a more capable Arduino compatible processor, like a [Teensy 4](https://www.pjrc.com/store/teensy41.html) or a [Nano Sense 33](https://store-usa.arduino.cc/products/nano-33-ble-sense-rev2).

## Overview video

A video overview of the process of using an Arduino with moteus can be found here:

{{ youtube("dbV0jIN8Ay4") }}

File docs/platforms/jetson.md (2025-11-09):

# Nvidia Jetson Setup

Many (maybe all) NVIDIA Jetson boards include an onboard CAN-FD controller.  However, very few NVIDIA Jetson carrier boards include a CAN-FD transceiver.  The former manages the logic level CAN-FD protocol, the latter translates to the electrical wire interface and both are required.

There are three major options for communicating with moteus controllers from an NVIDIA Jetson board:

1. **USB Adapter**: A mjcanfd-usb-1x or similar USB adapter can be used.  This is simple and relatively convenient, although is bulky and can be unreliable in systems that experience physical vibration or EMI.

2. **PCIe/m.2 Adapter**: Many Jetson boards have an accessible m.2 slot.  These can be used with adapters like the [PEAK m.2 CAN-FD adapter](https://www.peak-system.com/PCAN-M-2.473.0.html?&L=1).  Do note that some Jetson carrier boards have an m.2 adapter, but it is physically mounted in such a way that precludes using the PEAK adapter specifically because mechanical interference would result.

3. **Onboard Jetson Controller**: To use this, you either need a carrier board with a CAN-FD transceiver, or you must connect an external transceiver to the appropriate pins.

For option 2 or 3, you then configure the CAN-FD interface using the same method as for any socketcan device.  That reference is here:

- [socketcan Configuration](../platforms/socketcan.md)

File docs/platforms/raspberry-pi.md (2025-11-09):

# Raspberry Pi Installation #

The non-gui moteus library will work on a Raspberry Pi out of the box:

```
python -m venv --system-site-packages moteus-venv
source moteus-venv/bin/activate
pip install moteus
```

However, neither pypi nor piwheels has a functioning pyside2 library,
which is needed for `moteus_gui`, and thus tview.  Fortunately, it is
packaged in Raspberry Pi OS.  To use that version, you can do the
following:

```
sudo apt install python3-pyside2* python3-serial python3-can python3-matplotlib python3-qtconsole

source moteus-venv/bin/activate
pip install asyncqt importlib_metadata pyelftools
pip install --no-deps moteus moteus_gui
```

# Running moteus_tool and tview #

pi3hat specific options for these tools are documented at https://github.com/mjbots/pi3hat/blob/master/docs/reference.md#usage-with-client-side-tools

Note that to use the pi3hat, all python scripts must be run as root.
Using sudo is one mechanism to do so:

```
source moteus-venv/bin/activate
pip install moteus-pi3hat

sudo moteus-venv/bin/tview
```

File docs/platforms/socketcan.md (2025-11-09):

# socketcan

Many CAN-FD adapters can be used with the Linux socketcan subsystem.  This section describes how to configure them for use with moteus:

## Bit Timings

To communicate with moteus, both the bitrate *AND* sample point *AND* sjw/dsjw must be configured for the socketcan device.  The following command will work with most devices:

```
ip link set can0 up type can \
  bitrate 1000000 dbitrate 5000000 \
  sjw 10 dsjw 5 \
  sample-point 0.666 dsample-point 0.666 \
  restart-ms 1000 fd on
```

Some devices will give an error if the `sjw` or `dsjw` options are too large.  In that case, select the largest possible `sjw` or `dsjw` option.

## Incompatible adapters

CAN-FD adapters that use the slcan protocol, or that are derived from canable hardware whether or not they use the slcan or candelight firmware, are known to be currently incompatible with moteus controllers.

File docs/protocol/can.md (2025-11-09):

# CAN Protocol

The register command set is intended for use in real-time
applications.  It provides multiple levels of conciseness, and is
possible to operate at over 1kHz on the provided FD-CAN communications
bus.

Common definitions:

- *endian-ness*: All primitive types are in least significant byte
  first
- *varuint*: A sequence of one or more uint8 values, in least
  significant byte first order.  For each value, the 7 LSBs contain
  data and if the MSB is set, it means there are more bytes remaining.
  At most, it may represent a single uint32 and thus 5 bytes is the
  maximum valid length.
- *float*: An IEEE 754 32-bit floating point number.

## CAN Format

Communication with moteus is conducted via CAN-FD frames with a 1Mbit
standard bitrate and a 5Mbit data bitrate.

### CAN ID

The ID is structured as a 16 bit number, with the high 8 bits being
the "source" and the low 8 bits being the "destination".  The
destination is the 7 bit servo ID with 0 as the highest bit.  The
source is an arbitrary 7 bit number, with the high bit being 1 if
moteus should reply to the message.

The CAN frame must be an extended one if the ID would be greater than
0x7fff, but otherwise whether or not a frame is extended is not
considered.

Example:

ID: 0x8001
 * Send from source 0
 * To destination 1
 * 16th bit is set, so a reply is requested

ID: 0x100
 * Send from source 1
 * To destination 0
 * No reply is requested

### Subframes

Each CAN-FD frame contains one or more "subframes".  A short
description of the allowable subframe types are described below.  The
canonical reference is located at
[multiplex/format.h](https://github.com/mjbots/mjlib/blob/master/mjlib/multiplex/format.h)

Any extra trailing padding bytes required in the CAN-FD frame should
be set to NOP (0x50).

#### Write Registers

*0x00, 0x04, 0x08, 0x0c* - write (int8|int16|int32|float)

- `varuint` => number of registers (may be optionally encoded as a
  non-zero 2 LSBS of the subframe type)
- `varuint` => start register number
- N x (int8|int16|int32|float) => values

#### Read Registers

*0x10, 0x14, 0x18, 0x1c* - read (int8|int16|int32|float)

- `varuint` => number of registers (may be optionally encoded as a non-zero 2 LSBs)
- `varuint` => start register number

#### Reply

*0x20, 0x24, 0x28, 0x2c* - reply (int8|int16|int32|float)

- `varuint` => number of registers (may be optionally encoded as a non-zero 2 LSBs)
- `varuint` => start register number
- N x (int8|int16|int32|float) => values

#### Errors

*0x30, 0x31* - write/read error

- `varuint` => register number
- `varuint` => error number

#### NOP

*0x50* - no operation

## Example

A single CAN-FD frame can be used to command the servo, and initiate a
query of certain registers.  An example frame might look like the
following, encoded in hex with annotations.

- `01` - write a single int8 register (number of registers is encoded
  in the 2 LSBs)
 - `00` - start register number "Mode"
 - `0a` - "position" mode
- `07` - write 3x int16 registers (number of registers is encoded in
  the 2 LSBs)
 - `20` - register 0x020
 - `6000` - position = 0x0060 = 96 = 3.456 degrees
 - `2001` - velocity = 0x0120 = 288 = 25.92 dps
 - `50ff` - feedforward torque = 0xff50 = -176 = 1.76 N*m
- `14` - read int16 registers
 - `04` - read 4 registers
 - `00` - starting at 0x000 (so 0x000 Mode, 0x001 Position, 0x002
   Velocity, 0x003 Torque)
- `13` - read 3x int8 registers
 - `0d` - starting at 0x00d (so 0x00d Voltage, 0x00e Temperature,
    0x00f Fault code)

Thus the whole CAN-FD message would be (in hex):

`01000a07206000200150ff140400130d`

To send this using the fdcanusb converter to a device configured at
the default address of 1, you could write.

`can send 8001 01000a07206000200150ff140400130d`

The `80` in ID is used for two purposes.  The high bit being set
forces the device to respond (otherwise it will not respond, even if
query commands are sent).  The remaining bits are the "ID" to respond
to.  In response to this command, a possible response from the servo
would look like:

`rcv 100 2404000a005000000170ff230d181400`

Decoded, that means:

- `100` from device "1" to device "0"

- `24` reply with int16 values
 - `04` 4 registers
 - `00` starting at register 0
 - `0a00` in mode 10 - Position
 - `5000` position is 0x0050 = 80 = 2.88 degrees
 - `0001` velocity is 0x0100 = 256 = 23.04 dps
 - `70ff` torque is 0xff70 = -144 = -1.44 Nm
- `23` reply with 3 int8 values
 - `0d` starting at register 0x00d
 - `18` voltage is 12V
 - `14` temperature is 20C
 - `00` no fault

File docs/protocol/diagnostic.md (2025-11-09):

# Diagnostic Protocol

The following command set is intended for debugging and diagnostics.
It can be entered from `tview` or the `--console` mode of
`multiplex_tool` or `moteus_tool`.

## `d` - board debug

### `d stop`

This causes the controller to enter the "stopped" state, which
disables the motor driver.

### `d raw`

This enters the "raw" PWM mode.  Syntax:

```
d raw <pwm_a> <pwm_b> <pwm_c>
```

Where the pwm values are between 0.0 and 1.0.  A command to the idle
state is thus: `d raw 0.5 0.5 0.5`.

### `d pwm`

This enters voltage-FOC mode.  Syntax:

```
d pwm <phase> <magnitude> [<phase_rate>]
```

Where phase is in radians, magnitude is in volts, and the optional
phase rate is in radians per second.

### `d dq`

This enters the current controlled FOC mode.  Syntax:

```
d dq <d_A> <q_A>
```

### `d pos`

This enters the position control FOC mode.  Syntax:

```
d pos <pos> <vel> <max_torque> [options...]
```

Each optional element consists of a prefix character followed by a value.  Permissible options are:

- `p` - kp scale: the configured kp value is multiplied by this
  constant for the duration of this command
- `d` - kd scale: the configured kd value is multiplied by this
  constant for the duration of this command
- `i` - ki ilimit scale: the configured ilimit value is multiplied by
  this constant for the duration of this command
- `s` - stop position: when a non-zero velocity is given, motion stops
  when the control position reaches this value.
- `f` - feedforward torque in Nm
- `t` - timeout: If another command is not received in this many
  seconds, enter the timeout mode.
- `v` - velocity limit: the given value will override the global
  velocity limit for the duration of this command.
- `a` - acceleration limit: the given value will override the global
  acceleration limit for the duration of this command.
- `o` - fixed voltage override: while in affect, treat the control as
  if `fixed_voltage_mode` were enabled with the given voltage
- `c` - fixed current override: while in affect, treat the control
  like `fixed_voltage_mode`, but instead commanding a fixed current.
- `b` - if non-zero, then ignore all `servopos` position bounds

The position, velocity, maximum torque, and all optional fields have
the same semantics as for the register protocol documented above.

### `d tmt`

Enter the timeout mode.  This mode commands a zero velocity and can only be exited through the stopped state.

```
d tmt <pos> <vel> <max_torque> [options...]
```

Available options are identical to `d pos`.

### `d zero`

Enter the zero velocity state.  A zero velocity is commanded
regardless of position.

```
d zero <pos> <vel> <max_torque> [options...]
```

Available options are identical to `d pos`.  `pos` and `vel` are
ignored.

### `d within`

Enter the "stay within" state.  When the position is contained within
the given bounds, only the feedforward torque is applied.  Otherwise,
the position mode controller is used to hold the position at the
violated boundary.

```
d within <lowbound> <highbound> <max_torque> [options...]
```

The fields have the same semantics as for the register protocol
documented above.  The options are largely the same as for `d pos`.
Unsupported options include:

 * `s` - stop position
 * `o` - fixed voltage override
 * `c` - fixed current override

### `d brake`

Enter the "brake" state.  In this mode, all motor phases are shorted
to ground, resulting in a passive "braking" action.

### `d nearest`

Update the current position to the closest one which is consistent
with a given output position.

```
d rezero <position>
```

### `d exact`

Update the current position to exactly the given value.

```
d exact <position>
```

### `d req-reindex`

Reset the homing state to relative based, requiring any homing
procedure to be re-run.

```
d req-reindex
```

### `d recapture`

When in position mode, reset the control position and velocity to the
currently sensed values.

```
d recapture
```

### `d cfg-set-output`

Modify the configuration as required so that the current observed
position will be equal to the given value.  Note, the configuration is
not written to persistent storage.

```
d cfg-set-output <position>
```

### `d cal`

INTERNAL moteus_tool USE ONLY: Enter the encoder calibration mode.
Upon starting this command, the controller will spin the motor in
voltage-FOC mode until the encoder covers a full revolution, then
repeat the process in the other direction.  During the process, the
current commanded phase and encoder value are periodically emitted to
the console.

Syntax:

```
d cal <magnitude> [options...]
```

Each optional element consists of a prefix character followed by a value.  Permissible options are:

* `s` - calibration speed in electrical revolutions per second

NOTE: This command is for internal moteus_tool use only.  It performs
only part of the calibration process, and saves nothing to the
persistent storage.

### `d flash`

Enter the bootloader.

NOTE: This is only intended for internal use.  Users who want to flash new firmware should use `moteus_tool`.

## `aux[12]` - Aux port manipulation

All commands are supported on both `aux1` and `aux2`.

### `aux1 out` - Set GPIO Output Values

```
aux1 out <data>
```

'data' is a single decimal integer.  Only bits associated with pins
configured as digital outputs are used, the remainder are ignored.

### `aux1 pwm` - Set PWM Output Values

```
aux1 pwm <pin> <value>
```

'pin' is a number from 0 to 4 that gives the pin to set.

'value' is a floating point value between 0.0 and 1.0 that gives the
output duty cycle for the pin.

### `aux1 ic-cmd` - Initiate an iC-PZ command

```
aux1 ic-cmd <HEXBYTE>
```

An example of entering analog mode calibration.

```
aux1 ic-cmd B0
```

### `aux1 ic-wr` - Write iC-PZ register

```
aux1 ic-wr <reg> <data>
```

Register is one byte in hex, data is 1 or more bytes in hex.

Example of switching to memory page 0.

```
aux1 ic-wr 40 00
```

### `aux1 ic-rd` - Read iC-PZ register

```
aux1 ic-rd <reg> <length>
```

The register is one byte in hex, length is a decimal value indicating
the number of bytes to read.

Example of reading the temperature data:

```
aux1 ic-rd 4e 2
```

### `aux1 ic-extra` - Select alternate periodic data

```
aux1 ic-extra <fields>
```

"fields" is a decimal bitmask of items to read at 1000Hz and display
in the diagnostic stream.

bit 0 - the diagnosis command result
bit 1 - the contents of the AI_PHASES registers

Example of enabling the AI_PHASES registers only:

```
aux1 ic-extra 2
```

## `tel` - telemetry

### `tel get`

Retrieve the contents of a given channel.  Text or binary mode is
determined via the `tel fmt` or `tel text` commands, and defaults to
binary mode.

```
tel get <channel>
```

### `tel list`

List all available telemetry channels.

### `tel schema`

Report the binary schema associated with the given channel.

```
tel schema <channel>
```

The schema is reported as follows:

```
emit <channel>\r\n
<LE uint32 size><data>
```

### `tel rate`

Control the rate at which a given channel is emitted.

```
tel rate <channel> <rate_ms>
```

### `tel fmt`

Select whether a given channel will be emitted in binary or text form.

```
tel fmt <channel> <format>
```

`format` is an integer, non-zero signifies the data should be emitted
as text.

### `tel stop`

Stop emitting all periodic telemetry data.

### `tel text`

Switch all channels to text mode.

## `conf` - configuration

NOTE: Any commands that change parameters, such as `conf set`, `conf
load`, or `conf default`, if executed manually in `tview` will not
automatically update the UI.  `tview` must be restarted to display the
new parameters in the UI.

### `conf enumerate`

Print the current value of all configurable parameters.

### `conf get`

Get the value of a single configurable parameter.

```
conf get <item>
```

### `conf set`

Set the value of a single configurable parameter in RAM.

```
conf set <item> <value>
```

### `conf load`

Load all configurable values from persistent storage.  This will
overwrite their current values in RAM.

### `conf write`

Write the current value of all configurable parameters from RAM to
persistent storage.

### `conf default`

Update the RAM values of all configurable parameters to their firmware
default.

NOTE: This only updates RAM, not the persistent storage.  A `conf
write` will be necessary to save these to persistant storage.

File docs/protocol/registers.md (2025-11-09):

# Register Reference

## Register Usage

Each register may be accessed as potentially multiple data types.
This section describes the common mappings, and the semantics of each
register.

### Mappings

When registers are accessed as integer types, the following mappings
are used to encode the underlying floating point values into integer
values.

#### Current (measured in Amps)

- int8 => 1 LSB => 1A
- int16 => 1 LSB => 0.1A
- int32 => 1 LSB => 0.001A

#### Torque (measured in N*m)

- int8 => 1 LSB => 0.5 N*m
- int16 => 1 LSB => 0.01 N*m
- int32 => 1 LSB => 0.001 N*m

#### Voltage (measured in Volts)

- int8 => 1 LSB => 0.5V
- int16 => 1 LSB => 0.1V
- int32 => 1 LSB => 0.001 V

#### Temperature (measured in degrees Celsius)

- int8 => 1 LSB => 1 C
- int16 => 1 LSB => 0.1C
- int32 => 1 LSB => 0.001 C

#### Time (measured in seconds)

- int8 => 1 LSB => 0.01s
- int16 => 1 LSB => 0.001s
- int32 => 1 LSB => 0.000001s

#### Position (measured in revolutions)

- int8 => 1 LSB => 0.01 rotation => 3.6 degrees (range of -1.27 to 1.27)
- int16 => 1 LSB => 0.0001 rotation => 0.036 degrees (range of -3.2767 to 3.2767)
- int32 => 1 LSB => 0.00001 rotation => 0.0036 degrees

#### Velocity (measured in revolutions / s)

- int8 => 1 LSB => 0.1Hz / 36 dps
- int16 => 1 LSB => 0.00025 Hz > 0.09 dps
- int32 => 1 LSB => 0.00001 Hz => 0.0036 dps

#### Acceleration (measured in revolutions / s^2)

- int8 => 1 LSB => 0.05 l/s^2
- int16 => 1 LSB => 0.001 l/s^2
- int32 => 1 LSB => 0.00001 l/s^2

#### PWM and kp/kd scale (unitless)

- int8 => 1 LSB => (1/127) - 0.007874
- int16 => 1 LSB => (1/32767) - 0.000030519
- int32 => 1 LSB => (1/2147483647) - 4.657e-10

#### Power (W)

- int8 => 1 LSB => 10.0 W
- int16 => 1 LSB => 0.05 W
- int32 => 1 LSB => 0.0001 W

## Registers

### 0x000 - Mode

Mode: Read/write

The current operational mode of the servo.  Not all values are valid
to write.

- 0 => stopped = writeable, clears faults
- 1 => fault
- 2,3,4 => preparing to operate
- 5 => PWM mode
- 6 => voltage mode
- 7 => voltage FOC
- 8 => voltage DQ
- 9 => current
- 10 => position
- 11 => timeout
- 12 => zero velocity
- 13 => stay within
- 14 => measure inductance
- 15 => brake

When sending a command, this register must be written before any other
registers in the command frame.

### 0x001 - Position

Mode: Read only

The current position of the servo, measured in rotations of the output
shaft.  The maximum negative integer is reserved and will not be
reported.

### 0x002 - Velocity

Mode: Read only

The current velocity of the servo, measured in Hz at the output shaft.

### 0x003 - Torque

Mode: Read only

The current applied torque as measured at the output shaft.

### 0x004 - Measured Q phase current

Mode: Read only

The current in the Q phase measured in amperes.

### 0x005 - Measured D phase current

Mode: Read only

The current in the D phase measured in amperes.

### 0x006 - Measured absolution position

Mode: Read only

If an absolute encoder is configured on the ABS port, its value will
be reported here in revolutions.

### 0x007 - Measured electrical power

Mode: Read only

The estimated electrical power applied to the motor if positive.  If
negative, power applied to the DC input bus.

### 0x00a - Motor temperature

Mode: Read only

The current motor temperature, measured in degrees celsius.  This will
only be valid if an NTC thermistor is connected to the TEMP pads,
`servo.motor_thermistor_ohm` is set to the correct resistance, and
`servo.enable_motor_temperature` is set to 1.

### 0x00b - Trajectory complete

Mode: Read only

Non-zero if the current acceleration or velocity limited trajectory is
complete, and the controller is following the final velocity.

### 0x00c - Home state

Mode: Read only

* 0 - *relative only* - the position is not referenced to anything
* 1 - *rotor* - the position is referenced to the rotor
* 2 - *output* - the position has been referenced to the output,
  either with an output referenced encoder, or with a "set output
  nearest" or "set output exact" command

### 0x00d - Voltage

Mode: Read only

The current input voltage.

### 0x00e - Temperature

Mode: Read only

The current board temperature, measured in degrees celsius.

### 0x00f - Fault code

Mode: Read only

A fault code which will be set if the primary mode is 1 (Fault).

* 32 - *calibration fault* - the encoder was not able to sense a
  magnet during calibration
* 33 - *motor driver fault* - the most common reason for this is
  undervoltage, moteus attempted to draw more current than the supply
  could provide.  Other electrical faults may also report this error,
  the `drv8323` diagnostic tree has more information.
* 34 - *over voltage* - the bus voltage exceeded `servo.max_voltage`.
  This can happen due to misconfiguration, or if the controller
  regenerated power with a supply that cannot sink power and no flux
  braking was configured.
* 35 - *encoder fault* - the encoder readings are not consistent with
  a magnet being present.
* 36 - *motor not configured* - the `moteus_tool --calibrate`
  procedure has not been run on this motor.
* 37 - *pwm cycle overrun* - an internal firmware error
* 38 - *over temperature* - the maximum configured temperature has
  been exceeded
* 39 - *outside limit* - an attempt was made to start position control
  while outside the bounds configured by `servopos.position_min` and
  `servopos.position_max`.
* 40 - *under voltage* - the voltage was too low
* 41 - *config changed* - a configuration value was changed during
  operation that requires a stop
* 42 - *theta invalid* - no valid commutation encoder is available
* 43 - *position invalid* - no valid output encoder is available
* 44 - *driver enable fault* - the MOSFET gate driver could not be
  enabled
* 45 - *stop position deprecated* - an attempt was made to use the
  deprecated "stop position" feature along with velocity or
  acceleration limits.  Prefer to instead command the desired position
  directly with a target velocity of 0.0, or secondarily, disable
  acceleration and velocity limits.
* 46 - *timing violation* - internal checks are enabled, and the
  controller violated an internal timing constraint
* 47 - *bemf feedforward no accel* - `servo.bemf_feedforward` is
  configured, but no acceleration limit was specified.  If you
  *really* know what you are doing, you can disable this with
  `servo.bemf_feedforward_override`.
* 48 - *invalid limits* - `servopos.position_min` or
  `servopos.position_max` are finite and outside the available
  position range

Some non-zero codes can be presented during valid control modes
without a fault.  These indicate which, if any, function is limiting
the output power of the controller.

* 96 - `servo.max_velocity`
* 97 - `servo.max_power_W`
* 98 - the maximum system voltage
* 99 - `servo.max_current_A`
* 100 - `servo.fault_temperature`
* 101 - `servo.motor_fault_temperature`
* 102 - the commanded maximum torque
* 103 - `servopos.position_min` or `servopos.position_max`

### 0x010 / 0x011 / 0x012 - PWM phase A / B / C

Mode: Read/write

When in Pwm mode, this controls the raw PWM value for phase A, B, and
C.  If unspecified, 0.0 is used.

### 0x014 / 0x15 / 0x16 - Voltage phase A / B / C

Mode: Read/write

When in Voltage mode, this controls the voltage applied to phase A,
B, and C.  If unspecified, 0.0 is used.

### 0x018 - Voltage FOC Theta

Mode: Read/write

When in Voltage Foc mode, this controls the desired electrical phase.
Integral types use the PWM mapping.  If unspecified, 0.0 is used.

### 0x019 - Voltage FOC Voltage

Mode: Read/write

When in Voltage Foc mode, this controls the desired applied phase
voltage.  If unspecified, 0.0 is used.

### 0x01a - D Voltage

Mode: Read/write

When in Voltage Dq mode, this controls the desired applied D voltage.
If unspecified, 0.0 is used.

### 0x01b - Q Voltage

Mode: Read/write

When in kVoltageDq mode, this controls the desired applied Q voltage.
If unspecified, 0.0 is used.

### 0x01c - Commanded Q Phase Current

Mode: Read/write

When in Current mode, this controls the desired Q phase current.  If
unspecified, 0.0 is used.

### 0x01d - Commanded D Phase Current

Mode: Read/write

When in Current mode, this controls the desired D phase current.  Unless
you like burning power, with a BLDC motor you will typically want this
set to 0.  If unspecified, 0.0 is used.

### 0x1e - Voltage FOC Theta Rate

Mode: Read/write

When in Voltage Foc mode, this controls the rate of change of
electrical phase.  Integral types use the velocity mapping.

### 0x020 - Position command

Mode: Read/write

When in Position mode, this controls the desired position.

The maximally negative integer, or NaN for float represents, "use the
current position value".

If unspecified, 0.0 is used.

Note, in the absence of any configured or commanded velocity or
acceleration limits, the controller will attempt to achieve this
position *right now* subject to the kp and kd constants.

### 0x021 - Velocity command

Mode: Read/write

When in Position mode, advance the desired position at the given
velocity in Hz.

As a special case, if the 0x020 position is unset, and 0x026 stop
position is set, the sign of this is ignored, and is instead selected
so that the motor will move towards the stop position.

The maximally negative integer, or NaN for float, is treated the same
as 0.0.

If unspecified, 0.0 is used.

### 0x022 - Feedforward torque

Mode: Read/write

When in Position mode, add the given feedforward torque after applying
all regular control loops.  Note, this is torque at the output shaft.
If unspecified, 0.0 is used.

### 0x023 - Kp scale

Mode: Read/write

When in Position mode, shrink the proportional control term by the
given factor.  Integral types are applied as for PWM.  If unspecified,
1.0 is used.

### 0x024 - Kd scale

Mode: Read/write

When in Position mode, shrink the derivative control term by the given
factor.  Integral types are applied as for PWM.  This is internally
limited to be no more than the kp scale.  If unspecified, 1.0 is used.

### 0x025 - Maximum torque

When in Position mode, the maximum torque to be applied.  If
unspecified, this defaults to the system-wide configured maximum
torque.

### 0x026 - Commanded stop position

When in Position mode, and a non-zero velocity is commanded, stop
motion when reaching the given position.  NaN / maximally negative
means no limit is applied.  If unspecified, NaN is used.

Note, if the controller is ever commanded to move *away* from the stop
position, say with a velocity command that is inconsistent with the
start and stop position, then it will act as if a 0 velocity has been
commanded and the current command position equals the stop position.

### 0x027 - Watchdog timeout

Mode: Read/write

This determines the length of time for which this command is valid.
If this timeout expires before another command is received, the
controller will enter the Timeout state.  The default is 0.0, which
means to use the system-wide configured default.  NaN / maximally
negative means apply no enforced timeout.

### 0x028 - Velocity limit

Mode: Read/write

This can be used to override the global velocity limit for internally
generated trajectories.

If negative, then no limit is applied.

If unspecified, it is NaN / maximally negative, which implies to use
the global configurable default.

### 0x029 - Acceleration limit

Mode: Read/write

This can be used to override the global acceleration limit for
internally generated trajectories.

If negative, then no limit is applied.

If unspecified, it is NaN / maximally negative, which implies to use
the global configurable default.

### 0x02a - Fixed voltage override

Mode: Read/write

If specified and not-NaN, then the control mode will temporarily be in
the "fixed voltage" mode, regardless of the current setting of
`servo.fixed_voltage_mode`.

### 0x02b - Ki ilimit scale

Mode: Read/write

When in Position mode, shrink the integral term's windup limit by the
given factor.  Integral types are applied as for PWM.  If unspecified,
1.0 is used.

### 0x02c - Fixed current override

Mode: Read/write

If specified, then the control mode will temporarily be in the "fixed
current" mode.  This is parallel to "fixed voltage" mode, but instead
of a fixed voltage, a fixed D axis current is controlled.

### 0x02d - Ignore position bounds

Mode: Read/write

If specified and non-zero, `servopos.position_min` and
`servopos.position_max` will be ignore.

### 0x030 - Proportional torque

Mode: Read

This reports the torque contribution from the proportional term in the
PID controller.

### 0x031 - Integral torque

Mode: Read

This reports the torque contribution from the integral term in the
PID controller.

### 0x032 - Derivative torque

Mode: Read

This reports the torque contribution from the derivative term in the
PID controller.

### 0x033 - Feedforward torque

Mode: Read

This reports the feedforward contribution in the PID controller.

### 0x034 - Total control torque

Mode: Read

This reports the total commanded torque from the position mode
controller.  This is also reported in 0x03a.

### 0x038 - Control Position

Mode: Read

This reports the current trajectory control position, in modes where
that is valid.  When velocity or acceleration limiting is enabled, the
control position will follow the desired limits to achieve the command
position.

### 0x039 - Control Velocity

Mode: Read

This reports the current velocity control value, in modes where that
is valid.  When velocity or acceleration limiting is enabled, the
control velocity will follow the desired limits to achieve the control
position and velocity.

### 0x03a - Control Torque

Mode: Read

The torque commanded by the control loop.  This is the same as 0x034.

### 0x03b - Position Error

Mode: Read

The current sensed position minus the control position.

### 0x03c - Velocity Error

Mode: Read

The current sensed velocity minus the control velocity.

### 0x03d - Torque Error

Mode: Read

The current sensed torque minus the control torque.

### 0x040 - Stay within lower bound

Mode: Read/write

When in Stay Within mode, this controls the minimum allowable
position.  The maximally negative integer or NaN for float represents,
"there is no lower bound".  When special or the position is above this
bound (and also respecting the optional upper bound), only a
feedforward torque is applied.  When outside this bound, the PID
controller is used to force the position back to the bound.  If
unspecified, 0.0 is used.

### 0x041 - Stay within upper bound

Mode: Read/write

When in Stay Within mode, this controls the maximum allowable
position.  The maximally negative integer, or NaN for float
represents, "there is no upper bound". When special or the position is
below this bound (and also respecting the optional lower bound), only
a feedforward torque is applied.  When outside this bound, the PID
controller is used to force the position back to the bound.  If
unspecified, 0.0 is used.

### 0x042 - Feedforward torque

A shadow of the 0x022 register.

### 0x043 - Kp scale

A shadow of the 0x023 register.

### 0x044 - Kd scale

A shadow of the 0x024 register.

### 0x045 - Maximum torque

A shadow of the 0x025 register.

### 0x046 - Watchdog timeout

A shadow of the 0x027 register.

### 0x047 - Ki ilimit scale

A shadow of the 0x02b register.

### 0x048 - Ignore position bounds

A shadow of the 0x02d register.

### 0x050 - Encoder 0 Position

Mode: Read only

Reports the current filtered position of the encoder configured in
slot 0.

### 0x051 - Encoder 0 Velocity

Mode: Read only

Reports the current filtered velocity of the encoder configured in
slot 0.

### 0x052 - Encoder 1 Position

Mode: Read only

Reports the current filtered position of the encoder configured in
slot 1.

### 0x053 - Encoder 1 Velocity

Mode: Read only

Reports the current filtered velocity of the encoder configured in
slot 1.

### 0x054 - Encoder 2 Position

Mode: Read only

Reports the current filtered position of the encoder configured in
slot 2.

### 0x055 - Encoder 2 Velocity

Mode: Read only

Reports the current filtered velocity of the encoder configured in
slot 2.

### 0x058 - Encoder Validity

Mode: Read only

Returns a bitfield, where bit 0 indicates whether encoder 0 is active,
bit 1 indicates whether encoder 1 is active, etc.

| Bit | Value |
|-----|---|
| 0 | Source 0 Theta |
| 1 | Source 0 Velocity |
| 2 | Source 1 Theta |
| 3 | Source 1 Velocity |
| 4 | Source 2 Theta |
| 5 | Source 2 Velocity |

### 0x05c - Aux1 GPIO Command

Mode: Read/write

The current output command for any GPIOs configured as an output on
aux1 as a bitfield.  Not all bits may be used, as bit 0 is always for
pin 1, whether or not it is configured as a GPIO output.

### 0x05d - Aux2 GPIO Command

Mode: Read/write

The current output command for any GPIOs configured as an output on
aux2 as a bitfield.  Not all bits may be used, as bit 0 is always for
pin 1, whether or not it is configured as a GPIO output.

### 0x05e - Aux1 GPIO Status

Mode: Read only

The current input value of any GPIOs configured as an input on aux1 as
a bitfield.  Not all bits may be used, as bit 0 is always for pin 1,
whether or not it is configured as a GPIO input.

### 0x05f - Aux2 GPIO Status

Mode: Read only

The current input value of any GPIOs configured as an input on aux2 as
a bitfield.  Not all bits may be used, as bit 0 is always for pin 1,
whether or not it is configured as a GPIO input.

### 0x060/0x064 - Aux1 Analog Inputs

Mode: Read only

The current input value of any analog inputs configured on aux1.  The
registers are associated with pins 1-5, regardless of whether they are
configured as an analog input.  Each value is scaled as a PWM from 0
to 1.

### 0x068/0x06c - Aux2 Analog Inputs

Mode: Read only

The current input value of any analog inputs configured on aux2.  The
registers are associated with pins 1-5, regardless of whether they are
configured as an analog input.  Each value is scaled as a PWM from 0
to 1.

### 0x070 - Millisecond Counter

Mode: Read only

Increments once per millisecond.  It wraps at the maximum value for
the queried type to the minimum value for that type.  For floating
point types, it counts integers from 0 to 8388608.

### 0x071 - Clock Trim

Mode: Read/write

An integer which can trim the clock rate of the microprocessor on the
moteus controller.  Positive values speed it up and negative values
slow it down.  Each integer step roughly corresponds to a 0.25% change
in speed.

WARNING: Changing the speed affects all processes driven by the
microcontroller, including CAN communication.  Thus setting this to a
non-zero value may prevent future CAN communications.

### 0x076/0x07a - Aux1 PWM Outputs

Mode: Read/write

The current output PWM value for the given pin on Aux1.  PWM mapping
is used for integral types.

### 0x07b/0x07f - Aux2 PWM Outputs

Mode: Read/write

The current output PWM value for the given pin on Aux1.  PWM mapping
is used for integral types.

### 0x100 - Model Number

Name: Model Number
Mode: Read only

This returns a 32 bit model number.

### 0x101 - Firmware Version

Mode: Read only

This returns a 32 bit firmware version, encoded bytewise as
major.minor.micro.  i.e. 0x010304 is version 1.3.4

### 0x102 - Register map version

Mode: Read only

This returns a number that indicates how to interpret all registers.

### 0x110 - Multiplex ID

Name: Multiplex ID
Mode: Configurable

This controls the primary ID used to access the device over the
multiplex RS485 bus.  It can only be between 1 and 127.  (0 is
reserved as the broadcast address).

### 0x120 - 0x122 - Serial Number

Name: Serial Number
Mode: Read only

This returns a 96 bit serial number, least significant word first.

### 0x130 - Set Output Nearest

Mode: Write only

When sent, this causes the servo to select a whole number of internal
motor rotations so that the final position is as close to the given
position as possible.

### 0x131 - Set Output Exact

Mode: Write only

When sent, the servo will force the output position to be the exact
specified value.

### 0x132 - Require Reindex

Mode: Write only

When sent with any value, the servo will require that any index
position be re-located before control can begin.  Regardless, the
position will reset to an arbitrary value consistent with the current
encoder settings.

### 0x133 - Recapture Position and Velocity

Mode: Write only

When sent with any value, and if in "position" mode, the servo will
re-initialize the current control position and velocity to the sensed
values.  This also forces any pre-existing position integrative term
to zero.  It is expected that this will mostly be used when the
current applied torque is 0, either because of an in-place maximum
torque limit of zero, or because of an in-place kp and kd scale of
zero.

### 0x140 - Driver Fault 1

Mode: Read only

The exact bitfield reported by the motor driver in fault conditions
for fault register 1.  Up to 16 bits may be set.  This will only be
non-zero if the current mode is fault (1) and the fault code is 33
(motor driver fault).

### 0x141 - Driver Fault 2

Mode: Read only.

The exact bitfield reported by the motor driver in fault conditions
for fault register 2.  Up to 16 bits may be set.  This will only be
non-zero if the current mode is fault (1) and the fault code is 33
(motor driver fault).

### 0x150 - 0x153 - UUID

Name: UUID
Mode: Read only, int32 only

This returns a 128 bit UUID, this is the value printed on mjbots
packaging and returned by `moteus_tool --info`

### 0x154 - 0x157 - UUID Mask

Name: UUID
Mode: Write only, int32 only

If one or more of these fields are written, then the entire frame
after this point will be discarded unless the devices corresponding
UUID matches what was written.

### 0x158 UUID Mask Functional

Name: UUID Filter capable
Mode: Read only

Returns non-zero if the UUID mask is usable.

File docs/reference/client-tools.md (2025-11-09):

# Client Tools

## tview usage

tview can monitor and control 1 or more devices simultaneously.  It can be started with:

```
python3 -m moteus_gui.tview --target 1[,2,3]...
```

When running, the configuration for each can be modified in the left hand tab, and live telemetry values can be displayed or plotted from the right hand tab.  diagnostic mode commands may be issued in the bottom terminal window.

A simple command and scripting language beyond the diagnostic protocol is available within the tview terminal window.

### Communicating with a specific device

If more than one device is available, commands can be sent to a specific device by prefixing the command with `ID>`.  For instance, to send a stop command to ID #2, you can do:

```
2>d stop
```

The 'A' character can be used to send to all devices simultaneously.

```
A>d stop
```

### Sending multiple commands at once

The `&&` token may be used to separate individual commands, which will be issued back to back.  For instance:

```
1>d stop && 2>d stop
```

Will send the command to both devices.

### Delays

A delay may be inserted into a sequence of commands by entering an integer number of milliseconds prefixed by the colon (':') character.  For instance:

```
d pos nan 0.5 1 s0.5 && :1000 && d stop
```

Will command a position mode, wait 1s, then command a stop.

### Waiting for a trajectory to complete

A sequence of commands can be paused until a controller has finished
its trajectory using the `?` character.

```
d pos 0 0 nan a2 && ? && d pos 1 0 nan a2
```

Will move to position 0, wait until that motion is complete, then move
to position 1, all with an acceleration limit of 2.

Specific devices can be queried by following the question mark with an
ID number.

```
2>d pos 0 0 nan a2 && 1>d pos 10 0 0 nan a2 && ?2 && 2>d stop
```

## Calibration

Assuming your controller has firmware installed already, you can
calibrate the controller using the following procedure.

```
python3 -m moteus.moteus_tool --target 1 --calibrate
```

WARNING: Any attached motor must be able to spin freely.  It will be
spun in both directions and at high speed.

After calibrating for an entirely new type of motor, you may need to
adjust PID gains before the motor will perform acceptably, and/or
configure `motor_position.rotor_to_output_ratio`.

## Setting the "zero offset"

The moteus controller can locate positions within one revolution after being power cycled, and will start with the reported position being between -0.5 and 0.5.  The physical zero position can be set using the following command:

```
python3 -m moteus.moteus_tool --target 1 --zero-offset
```

## Configuring the CAN-FD transport

`moteus_tool` and `tview` can be configured to communicate with a
moteus controller through a variety of transports.  By default, it
will attempt to autodetect either a fdcanusb or socketcan interface.

To force usage of a particular fdcanusb, you can use:

```
python3 -m moteus.moteus_tool --fdcanusb /path/to/fdcanusb
```

To force a particular python-can method, you can use:

```
python3 -m moteus.moteus_tool --can-iface socketcan --can-chan can0
```

where `--can-iface` specifies the "interface" for python-can and
`--can-chan` specifies the "channel".

Note, these are in addition to any other `moteus_tool` or `tview`
options that may be desired.

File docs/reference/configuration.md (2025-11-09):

# Configuration Parameters

This section describes the configurable values which are most likely
to be modified for end-user applications.  Changes to all values take
effect *immediately*.  This may mean, that for instance, it is wise to
stop control loops before drastically changing control parameters.  Or
maybe not, it depends upon your goals.

## `id.id`

The servo ID presented on the CAN bus.  After this is modified, you need to immediately adjust which servo ID you communicate with in order to continue communication or save the parameters.

## `can.prefix`

A 13 bit integer used as the upper 13 bits for the ID of all CAN
communication.  As with `id.id` this takes effect immediately, so
after changing it, communication must be restarted with the correct
prefix in order to do things like save the configuration.

## `servopos.position_min`

The minimum allowed control position value, measured in rotations.  If
NaN, then no limit is applied.

## `servopos.position_max`

The maximum allowed control position value, measured in rotations.  If
NaN, then no limit is applied.

## `servo.pid_position`

These configure the position mode PID controller.

* `kp/ki/kd` - PID gains with units of:
  * kp - Nm per rotation
  * ki - Nm/s per rotation
  * kd - Nm per rotation/s
* `iratelimit` - The maximum rate at which the integral term can
   wind up, in N*m/s.  <0 means "no limit"
* `ilimit` - The total maximum I term, in Nm
* `max_desired_rate` - If non-zero, the commanded position is
  limited to change at this rate in Hz.

Note, these values are in physical units.  Thus a `kp` value of 1,
means that for 1 revolution of error at the output, 1 Nm of corrective
torque will be applied.  Similarly, with a `kd` value of 1, 1
revolution per second of error will result in 1 Nm of corrective
torque.  Doubly note that these values are measured at the output,
thus *after* any scaling in position, velocity, and torque implied by
`motor_position.rotor_to_output_ratio`.

## `servo.pid_dq`

These have the same semantics as the position mode PID controller, and
affect the current control loop.

## `servo.default_velocity_limit` / `servo.default_accel_limit`

Limits to be placed on trajectories generated within moteus.  If
either is `nan`, then that limit is unset.  The limits may also be
overriden individually on a per command basis.  The semantics of the
limits are as follows:

- *Neither set (both nan)* In this case, position and velocity
  commands take immediate effect.  The control position will be
  initialized to the command position, and the control velocity will
  be set to the command velocity.  The control position will advance
  at the given velocity indefinitely, or until the command stop
  position is reached.

- *Either set*: If x_c is the command position, v_c is the command
  velocity, and t is the time from receipt of the command, the
  semantics can be described as: "match the trajectory defined by x =
  x_c + v_c * t".

  If the acceleration limit is set, the above is effected by
  commanding accelerations of either [-accel_limit, 0, accel_limit].
  If an acceleration limit is not set, then the velocity will change
  instantaneously.

  If the velocity limit is set, then the intermediate velocities will
  obey "-velocity_limit < velocity < +velocity_limit".  If it is not
  set, then the velocities may grow to arbitrary magnitude.

NOTE: This is limited internally to be no more than
`servo.max_velocity`.

## `servo.inertia_feedforward`

When set to non-zero, and acceleration limits are currently in effect,
this will apply a feedforward torque equal to the current acceleration
multiplied by this configurable value.  This can be used to improve
response transients for short movements, where the acceleration period
is not long enough for the normal position PID to track well.

In an ideal world, you would set this to the moment of inertia of your
system in measured in kg * m^2.

## `servo.voltage_mode_control`

When set to non-zero, the current control loop is not closed, and all
current commands in amperes are instead treated as voltage mode
commands in volts related by the calibrated phase resistance.  For
high winding resistance motors, the default current sense resistors
are too small for accurate current sensing, resulting in significant
cogging torque and current sense noise.  If replacing the current
sense resistors is not an option, this flag can be used to achieve
smooth control.  The downside is that the actual torque will no longer
follow the applied torque accurately at speed, or in the face of
external disturbances.

When set, the `servo.pid_dq` configuration values no longer affect
anything.

## `servo.fixed_voltage_mode`

If non-zero, then no feedback based control of either position or
current is done.  Instead, a fixed voltage is applied to the phase
terminals based on the current commanded position and the configured
number of motor poles.  In this mode, the encoder and current sense
resistors are not used at all for control.

This is a similar control mode to inexpensive brushless gimbal
controllers, and relies on burning a fixed amount of power in the
motor windings continuously.

When this mode is active, the reported position and velocity will be 0
when the drive is disabled, and exactly equal to the control position
when it is enabled.

Various derating limits are inoperative in this mode:
 * torque derating for temperature
 * torque derating when outside position bounds
 * the maximum current limit
 * the commanded maximum torque

A fault will still be triggered for over-temperature.

## `servo.fixed_voltage_control_V`

In the fixed voltage control mode, the voltage to apply to the output.

## `servo.max_position_slip`

When finite, this enforces a limit on the difference between the
control position and the current measured position measured in
revolutions.  It can be used to prevent "catching up" when the
controller is used in velocity mode.

## `servo.max_velocity_slip`

When finite, this enforces a limit on the difference between the
control velocity and the current measured velocity, measured i Hz.  It
can be used to ensure that acceleration limits are obeyed in velocity
mode when external torques exceed the maximum.  If used, typically
`servo.max_position_slip` must be relatively small to avoid
instability.

## `servo.max_voltage`

If the input voltage reaches this value, a fault is triggered and all
torque is stopped.

## `servo.max_power_W`

If set, set the allowable maximum power to the lower of this and the
factory board power profile.

## `servo.override_board_max_power`

If true, then `servo.max_power_W` is used as the power limit even if
it is larger than the factory board power profile.

## `servo.pwm_rate_hz`

The PWM rate to use, defaulting to 30000.  Allowable values are
between 15000 and 60000.  Lower values increase efficiency, but limit
peak power and reduce the maximum speed and control bandwidth.

## `servo.derate_temperature`

Torque begins to be limited when the temperature reaches this value.

## `servo.fault_temperature`

If the temperature reaches this value, a fault is triggered and all
torque is stopped.

## `servo.enable_motor_temperature`

If true, then the motor temperature will be sensed via the TEMP pads
on the board.

## `servo.motor_derate_temperature`

Torque begins to be limited when the motor temperature reaches this value.

## `servo.motor_fault_temperature`

If the motor temperature reaches this value, a fault is triggered and
all torque is stopped.

## `servo.flux_brake_margin_voltage`

Selects the flux braking point relative to the currently configured `servo.max_voltage`.  `flux braking point = max_voltage - flux_brake_margin_voltage`.

When the input voltage is above the braking point, the controller
causes the motor to act as a "virtual resistor" with resistance
`servo.flux_brake_resistance_ohm`.  All extra energy is dumped into
the D phase of the motor.  This can be used to handle excess
regenerative energy if the input DC link is incapable of accepting
sufficient energy.

## `servo.max_current_A`

Phase current will never be used more than this value.  It can be
decreased to limit the total power used by the controller.  Increasing
beyond the factory configured value can result in hardware damage.

## `servo.max_velocity`

Output power will be limited if the velocity exceeds this threshold.

## `servo.max_velocity_derate`

Once velocity reaches the max_velocity plus this value, allowed output
power is reduced to 0.

## `servo.rotation_*`

These values configure a higher order torque model for a motor.

* `servo.rotation_current_cutoff_A` if the phase current is less than
  this value, then the linear relationship implied by `motor.v_per_hz`
  is used.

Once above that cutoff, the following formula is used to determine
torque from phase current:

```
torque = cutoff * tc + torque_scale * log2(1 + (I - cutoff) * current_scale)
```

Where `tc` is the torque constant derived from `motor.v_per_hz`.

This model is not automatically calibrated, and needs to be determined
and configured manually.

## `servo.default_timeout_s`

When sending position mode commands over CAN, there is an optional
watchdog timeout.  If commands are not received at a certain rate,
then the controller will latch into the "position timeout" state,
requiring a stop command to resume operation.  This configuration
value controls the length of time that the controller will wait after
receiving a command before entering this state.  If set to `nan` then
the controller will never enter this timeout state.

It may be overidden on a per-command basis with the 0x027 register or
the `t` optional flag of the `d pos` command for the diagnostic
interface.

## `servo.timeout_max_torque_Nm`

When in the "position timeout" mode the controller acts to damp the
output.  This parameter controls the maximum torque available for such
damping.

## `servo.timeout_mode`

Selects what behavior will take place in the position timeout mode.
The allowable values are a subset of the top level modes.

* 0 - "stopped" - the driver is disengaged
* 10 - "decelerate to 0 velocity and hold position"
* 12 - "zero velocity"
* 15 - "brake"

For mode 10, `servo.default_velocity_limit` and
`servo.default_accel_limit` are used to control the deceleration
profile to zero speed.  The default PID gains are used.  The only
limit on torque when in this timeout mode is `servo.max_current_A`.

## `servo.motor_thermistor_ohm`

The resistance of any attached motor NTC thermistor as measured at 25C
in ohms.

## `aux[12].pins.X.mode`

Selects what functionality will be used on the given pin.

* 0 - NC - Not connected (or used for onboard SPI)
* 1 - SPI - Used for one of CLK, MISO, or MOSI
* 2 - SPI CS - Used for SPI CS
* 3 - UART
* 4 - Software quadrature
* 5 - Hardware quadrature
* 6 - Hall
* 7 - Index
* 8 - Sine
* 9 - Cosine
* 10 - Step (not implemented)
* 11 - Dir (not implemented)
* 12 - RC PWM (not implemented)
* 13 - I2C
* 14 - Digital input
* 15 - Digital output
* 16 - Analog input
* 17 - PWM output

## `aux[12].pins.X.pull`

Configures optional pullup or pulldown on each pin.  Not all pullup
options will be used with every mode.  Additionally, the 2 aux2 pins
on moteus 4.5/8/11 have hard-installed 2k ohm pullups regardless of
these settings.

* 0 - no pullup or pulldown
* 1 - pull up
* 2 - pull down
* 3 - open drain (not implemented)

## `aux[12].i2c.i2c_hz`

The frequency to operate the I2C bus at.  Between 50000 and 400000.

## `aux[12].i2c.i2c_mode`

What I2C mode to use.

## `aux[12].i2c.devices.X.type`

What I2C device to expect.

* 0 - disabled
* 1 - AS5048
* 2 - AS5600

## `aux[12].i2c.devices.X.address`

The I2C address to use.

## `aux[12].i2c.devices.X.poll_ms`

How often in milliseconds to poll the device for more data.  Must no
less than 5.

## `aux[12].spi.mode`

The type of SPI device.

* 0 - The onboard AS5047P (CPR == 16384). Only valid for aux1.  If
  selected, the CLK, MOSI, and MISO lines must be either NC or
  selected as SPI.
* 1 - Disabled.
* 2 - AS5047P (CPR == 16384)
* 3 - iC-PZ
* 4 - MA732 (CPR == 65536)
* 5 - MA600 (CPR == 65536)
* 8 - AMT22 (CPR == 16384)

NOTE: iC-PZ devices require significant configuration and calibration
before use.  Diagnostic mode commands are provided for low level
access.

## `aux[12].spi.rate_hz`

The frequency to operate the SPI bus at.  The default is 12000000.

## `aux[12].uart.mode`

The type of UART device.

* 0 - Disabled
* 1 - RLS AksIM-2
* 2 - Tunnel
* 3 - Per-control cycle debug information (undocumented)
* 4 - CUI AMT21x series RS422

When the tunnel mode is selected, data may be sent or received using
the CAN diagnostic protocol.  For aux1, use diagnostic channel 2.  For
aux2, use diagnostic channel 3.

## `aux[12].uart.baud_rate`

The baud rate to use for the UART.

## `aux[12].uart.poll_rate_us`

For encoder modes, the interval at which to poll the encoder for new
position information.

## `aux[12].uart.rs422`

Enable the RS422 transceiver.  This is only valid for 'aux1', and
requires that pin D and E (`aux1.pins.3` and `aux1.pins.4`) be
used for UART.

## `aux[12].uart.cui_amt21_address`

Select the CUI AMT21 address to communicate with.  The default is 0x54
(84 decimal), which is the default address CUI AMT21 encoders are
configured with.

## `aux[12].quadrature.enabled`

True/non-zero if quadrature input should be read from this port.

## `aux[12].quadrature.cpr`

The number of counts per revolution of the quadrature input.  If used
as a source, then this CPR must match the one configured in the
source.

## `aux[12].hall.enabled`

True/non-zero if hall effect sensors should be read from this port.

## `aux[12].hall.polarity`

A bitmask to XOR with the 3 hall phases.

## `aux[12].index.enabled`

True/non-zero if an index input be read from this port.

## `aux[12].sine_cosine.enabled`

True/non-zero if a sine/cosine input should be read from this port.

## `aux[12].sine_cosine.common`

The common mode voltage to use for the sine cosine.  The sampling is
done with 12 bits, so 2048 would be exactly 0.5 * 3.3V.  However, it
is best to calibrate this with actual readings as observed over the
diagnostic protocol for optimal performance.

## `aux[12].i2c_startup_delay_ms`

A delay in milliseconds after power-on (or upon reconfiguring), before
I2C devices associated with this auxiliary port are first used.

## `aux[12].pwm_period_us`

The period in microseconds to be used for PWM outputs on this
auxiliary port.

## `motor_position.sources.X.aux_number`

1 for an aux1 device, or 2 for an aux2 device.

## `motor_position.sources.X.type`

One of:

* 0 - disabled
* 1 - SPI
* 2 - UART
* 3 - Quadrature
* 4 - Hall
* 5 - Index
* 6 - Sine/Cosine
* 7 - I2C
* 8 - Sensorless (not implemented)

Note: The "Index" source type is only allowed for an output referenced
encoder, and can be used as an alternate way to enter the "output"
homed state.

## `motor_position.sources.X.i2c_device`

If `type` was "7/I2C", this is a 0 based index specifying *which* I2C
device on that port should be used.

## `motor_position.sources.X.incremental_index`

If the specified auxiliary port has an incremental encoder, like a
quadrature encoder, this can be set to either 1 or 2 in order to use
an "index" pin to reference the data to a given position.  It will
allow the source to provide theta readings for commutation.

## `motor_position.sources.X.cpr`

The CPR of the given input.  In some cases this is automatically set,
but in most it will need to be manually entered.

## `motor_position.sources.X.offset/sign`

An integer offset and inversion to apply.  The resulting value is:
`(raw + offset) * sign / cpr`.

## `motor_position.sources.X.reference`

* 0 - this source is relative to the rotor
* 1 - this source is relative to the output

## `motor_position.sources.X.pll_filter_hz`

Selects the 3dB cutoff frequency of a low-pass filter used on this
source.  It should typically be less than 10X the update rate of the
input and if used as the commutation or output sensor, should be
higher than the mechanical bandwidth of the plant.  Within that range,
it can be tuned for audible noise versus performance.

If set to 0, then no filter is applied.  In that case, sensors which
do not natively measure velocity will produce no velocity readings
(most of them).
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

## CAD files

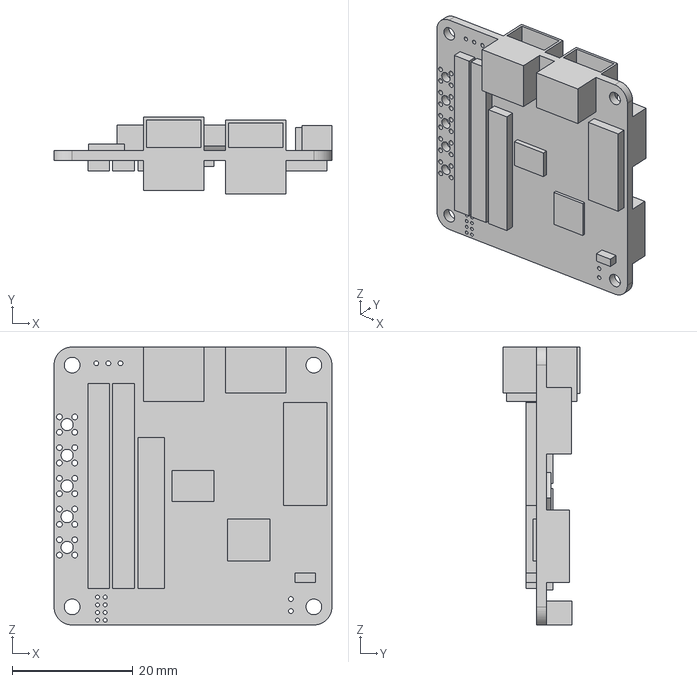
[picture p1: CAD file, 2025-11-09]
hw/n1_r1.3/20230523-moteus-n1-r1_3-mechanical.step
46.0 x 12.8 x 46.0 mm

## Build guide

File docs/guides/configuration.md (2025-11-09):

# Configuration

Before using a moteus controller for the first time, it is necessary to configure several key parameters. These parameters define operational limits, control behavior, and configure the system to match your specific application.

## Essential Configuration Parameters

The following parameters should be reviewed and will likely need to configured in a customized way for nearly every application.

### Position Limits

**`servopos.position_min` and `servopos.position_max`**

These define the bounds of motion which the controller will allow when in position control mode. Attempting to start beyond this region will fault, and if outside the region during operation, no torque will be applied to move further outside these limits.  If they are unwanted, `nan` should be used to disable them.

### Current Limits

**`servo.max_current_A`**

The maximum phase current to apply to the motor. This can be used to limit the maximum torque that the system is capable of producing, regardless of any command sent. Set this based on your motor's peak current rating and thermal capabilities.

### Velocity Limits

**`servo.max_velocity`**

Limits the maximum speed the motor is permitted to achieve before no torque is produced. This acts as a safety limit to prevent excessive speeds that could damage the motor or mechanical system.

**`servo.default_velocity_limit` / `servo.default_accel_limit`**

Controls how fast the motor can accelerate and spin in order to reach position and velocity targets. Bare boards ship with these unset, while development kits ship with human-eye pleasing values. Adjust these to match your application's performance requirements.

### Gearbox Scaling

**`motor_position.rotor_to_output_ratio`**

A gearbox scaling factor. A reducing gearbox should be configured with a number smaller than one (e.g., 0.25 for a 4x reduction gearbox). This affects reported position, speed, and torques, scaling them to represent the output shaft values rather than motor shaft values.

### Device Identification

**`id.id`**

The CAN-FD ID used by this device. Each controller on the bus must have a unique ID. Valid IDs range from 1 to 126.  If you set this to a value other than 1, be aware that unless your tview and controller firmware are newer than late 2025, you will need to restart tview with:

```
python -m moteus_gui.tview -t N
```

Where N is the new ID, in order to issue a `conf write` to save the
parameters.

### PID Parameters

**`servo.pid_position`**

The PID parameters for the position control loop. It will be necessary to tune these, it isn't hard, although it must be done after calibration is performed. You'll get to the [PID Tuning guide](../guides/pid-tuning.md) after completing the calibration process.

## Saving parameters

All parameters (including the ID) are temporarily stored in volatile memory that will be discarded after a power cycle.  To save those parameters to persistent storage, it is necessary to type:

```
conf write
```

Into the diagnostic console of tview.

## Additional Configuration

A larger set of parameters is documented in the [Configuration Parameters Reference](../reference/configuration.md), covering advanced features such as:

- Motor electrical characteristics
- Encoder configuration
- Temperature limits
- Communication settings
- Advanced control parameters

## Next Steps

After configuring these essential parameters, you should familiarize yourself with the encoder system and position feedback:

- [Encoder Overview](encoder-overview.md)

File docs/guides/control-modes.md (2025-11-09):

# Control Modes

The moteus controller offers flexible control modes to suit different robotics applications. By adjusting control gains and command parameters, you can optimize the controller for various use cases—from precise positioning and velocity control to high-bandwidth torque applications. This guide covers the recommended configurations for common control scenarios.

## Understanding Position Mode

The primary control mode for the moteus controller is an integrated position/velocity controller. The semantics of the control command are somewhat unorthodox, so as to be easily amenable to idempotent commands sent from a higher level controller. Each command includes the following parameters:

- **Position**: The desired position in revolutions
- **Velocity**: The rate at which the desired position changes in revolutions/s
- **Maximum torque**: Never use more than this amount of torque when controlling
- **Feedforward torque**: Give this much extra torque beyond what the normal control loop says
- **Stop position**: If non-special, never move the desired position away from this target
- **kp scale**: Scale the proportional constant by this factor
- **kd scale**: Scale the derivative constant by this factor
- **ilimit scale**: Scale the integrative limit by this factor
- **Velocity limit override**: If non-special, override the configured velocity limit, which constrains how quickly the target position is reached
- **Acceleration limit override**: If non-special, override the configured acceleration limit, which constrains how quickly the target position is reached

Additionally, the position may be set as a "special value" (NaN for floating point and the debug interface, maximal negative for integer encodings). In that case, the position selected is "wherever you are right now".

A pure velocity mode can be obtained by setting the kp scale to 0 (or permanently so by configuring the kp constant to 0). In this case, using the `servo.max_position_slip` configurable parameter may be valuable as per the velocity control section below.

## Velocity Control

To implement a velocity controller, each command should have the
"position" set to NaN (or equivalent integral encoding).  It is
recommended to configure `servo.max_position_slip` to a finite value
greater than or equal to 0 ([reference](../reference/configuration.md#servomax_position_slip)).
When it is larger, more external disturbances will be rejected, but
the controller will also "catch up" when the magnitude of external
disturbances is decreased.

**Example:**

=== "Diagnostic Protocol"

    ```
    d pos nan 2 nan
    ```

=== "Python"

    ```python
    await controller.set_position(
        position=math.nan,  # NaN for velocity mode
        velocity=2.0,       # 2 revolutions/second
        query=True
    )
    ```

=== "C++"

    ```cpp
    mjbots::moteus::PositionMode::Command cmd;
    cmd.position = std::numeric_limits<double>::quiet_NaN();
    cmd.velocity = 2.0;  // 2 revolutions/second

    auto result = controller.SetPosition(cmd);
    ```

## Constant Acceleration Trajectories

Velocity and acceleration limits can be configured either globally, or
on a per-command basis which will cause moteus to internally generate
continuous acceleration limited trajectories to reach the given
position and velocity.  Once the trajectory is complete, the command
velocity is continued indefinitely.

=== "Diagnostic Protocol"

    ```
    # Move to position 1 then stop.  Accelerate/decelerate at 2Hz/s
    # and use a maximum velocity of 0.5Hz.
    d pos 1 0 nan a2 v0.5
    ```

=== "Python"

    ```python
    await controller.set_position(
        position=1,
        velocity=0,
        accel_limit=2,
        velocity_limit=0.5,
    )
    ```

=== "C++"

    ```cpp
    mjbots::moteus::Controller::Options options;
    options.position_format.accel_limit = mjbots::moteus::kFloat;
    options.position_format.velocity_limit = mjbots::moteus::kFloat;

    mjbots::moteus::Controller controller(options);

    mjbots::moteus::PositionMode::Command cmd;
    cmd.position = 1.0;
    cmd.velocity = 0.0;
    cmd.accel_limit = 2.0;
    cmd_velocity_limit = 0.5;

    auto result = controller.SetPosition(cmd);
    ```

Default values for acceleration and velocity limits can also be set in
configuration.

* `servo.default_accel_limit`
* `servo.default_velocity_limit`

## Torque Control

For a pure torque control application, the PID gains of the position control loop must be set to 0.  One way to accomplish that is by sending the `kp_scale`, `kd_scale`, and `ilimit_scale` values to 0.

=== "Diagnostic Protocol"

    ```
    # Command a torque of 0.1 Nm
    d pos nan 0 nan p0 d0 i0 f0.1
    ```

=== "Python"

    ```python
    await controller.set_position(
        position=math.nan,
        velocity=0,
        kp_scale=0.0,
        kd_scale=0.0,
        ilimit_scale=0.0,
        feedforward_torque=0.1,
    )
    ```

=== "C++"

    ```cpp
    mjbots::moteus::Controller::Options options;
    options.position_format.kp_scale = mjbots::moteus::kFloat;
    options.position_format.kd_scale = mjbots::moteus::kFloat;
    options.position_format.ilimit_scale = mjbots::moteus::kFloat;
    options.position_format.feedforward_torque = mjbots::moteus::kFloat;

    mjbots::moteus::Controller controller(options);

    mjbots::moteus::PositionMode::Command cmd;
    cmd.position = std::numeric_limits<double>::quiet_NaN();
    cmd.velocity = 0.0;
    cmd.kp_scale = 0.0;
    cmd.kd_scale = 0.0;
    cmd.ilimit_scale = 0.0;
    cmd.feedforward_torque = 0.1;

    auto result = controller.SetPosition(cmd);
    ```

**Caveat**: Using external torque control will be much lower
bandwidth than using the internal position controller of moteus (~15x
lower bandwidth if maximal CAN-FD update rate is achieved).  Thus, a
system will usually perform better if as much of the desired control
law as possible is formulated in terms of the built in position
controller.

If the system will never perform anything *but* torque control, then the PID gains can be set to 0 in configuration.

* `servo.pid_position.kp`
* `servo.pid_position.kd`
* `servo.pid_position.ilimit`

## Jerk Limited Trajectories

moteus only supports acceleration limited internal trajectories.  To
approximate a constant jerk trajectory, the host processor should send
a sequence of piecewise linear constant velocity trajectories which
approximate the desired one.  This would be done by sending commands
consisting of at least a position and velocity at some moderate to
high rate while disabling the internal velocity and acceleration
limits.

## Low Speed or Precise Positioning

For either operation at very low speeds, or when precise positioning
performance is desired, it is recommended to configure a non-zero `ki`
and `ilimit` term in the position controller
([reference](../reference/configuration.md#servopid_position)).  This will compensate for cogging
torque (at the expense of overall torque bandwidth).  It may also be
beneficial to select a higher value for calibration bandwidth.

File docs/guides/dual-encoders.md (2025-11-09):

# Dual Encoder Configuration

Often moteus is used in applications where a gearbox or other reducer is used between the rotor and the final plant.  In those situations it can be valuable to have a secondary encoder measuring the output of the reducer:

**Absolute positioning**: With only an encoder on the rotor, it is not possible to know absolutely where the output is.

**Improved accuracy or sensing performance**: The onboard encoder included with moteus is sufficient for commutation for nearly all motors, however some applications may require lower position or velocity sensing noise or higher resolution in order to achieve accurate very slow movements, or very accurate positioning.

This section will cover how to set up several common dual encoder configurations.

## Important factors when configuring dual encoders

1. **Sign match**: moteus requires that the sign of all encoders match.  Those must be configured manually in `motor_position.sources.X.sign`.  To verify the signs are correct, plot `motor_position.sources.X.filtered_value` for all configured encoders, spin the system by hand, and verify that all plots move in the same direction.

2. **Offset match**: If the absolute values of multiple encoders must be related, such as for a disambiguation configuration, then the offsets must be matched so that the encoders read 0 at the same time.  These offsets must be manually configured in `motor_position.sources.X.offset`.  To verify they are correct, plot `motor_position.sources.X.filtered_value` for all configured encoders, spin the system by hand to the zero point, and verify that all encoders read 0.

## Onboard + 8x reducer + MA600 on-axis - Disambiguation

In this configuration, the rotor is sensed with the moteus onboard encoder and the output is sensed with an MA600 on-axis encoder.  Assuming low backlash, the output positioning is performed from the onboard encoder and the output encoder is only used for disambiguation.  This results in the best performance since the effective resolution of the onboard encoder is multiplied by the gear reduction and will be much better than the MA600 on the output.

The MA600 is attached to the aux2 port on one of the moteus-c1 [(c1 pinout)](../reference/pinouts.md#moteus-c1), moteus-n1 [(n1 pinout)](../reference/pinouts.md#moteus-n1), or moteus-x1 [(x1 pinout)](../reference/pinouts.md#moteus-x1).

This pinout is the one accomplished if using the cable included with the [mjbots MA600 breakout board](https://mjbots.com/products/ma600-breakout).

If starting from a factory default configuration, first, configure the
aux2 port:

```
aux2.pins.0.mode 1  # spi
aux2.pins.1.mode 1  # spi
aux2.pins.2.mode 1  # spi
aux2.pins.3.mode 2  # spi_cs
aux2.spi.mode 5     # ma600
aux2.spi.rate_hz 6000000
```

Then, configure motor_position:

```
motor_position.sources.1.aux_number 2
motor_position.sources.1.type 1
motor_position.sources.1.cpr 65536
motor_position.sources.1.reference 1  # output
motor_position.rotor_to_output_ratio 0.125
motor_position.output.reference_source 1
```

The sign and offset of the MA600 will need to be matched to the onboard encoder as per [the above section](#match).

## Onboard + 10x reducer + AksIM-2 on output

In this configuration, the onboard encoder is used to sense the rotor, and an AksIM-2 encoder from RLS is used on the output.  The AksIM-2 has much better accuracy and noise performance than the onboard on-axis encoder, and thus this configuration could be used for applications where either very accurate positioning is required, or very precise low speeds are required.

The AksIM-2 is attached to the GH-6 RS422 connector on a moteus-n1 [(n1 pinout)](../reference/pinouts.md#moteus-n1) or moteus-x1 [(x1 pinout)](../reference/pinouts.md#moteus-x1).

moteus is compatible with AksIM-2 encoders configured as follows:

- **Communication Interface**: SF - Asynchronous Serial, RS422, 5V
- **Communication Protocol Variant**: F - 1000 kbps
- **Resolution**: <= 19B, no multiturn support

If starting from a factory default configuration, first configure the aux1 port.

```
aux1.pins.4.mode 3 # uart
aux1.pins.5.mode 3 # uart
aux1.uart.mode 2 # aksim2
aux1.uart.baud_rate 1000000
aux1.uart.rs422 1
```

Then configure motor_position:

```
motor_position.rotor_to_output_ratio 0.1
motor_position.sources.1.aux_number 1
motor_position.sources.1.type 2          # uart
motor_position.sources.1.cpr 4194304     # used by moteus for all AksIM-2
motor_position.sources.1.reference 1     # output
motor_position.output_source 1
```

The sign and offset of the AksIM-2 will need to be matched to the onboard encoder as per [the above section](#match).

## Hall + 10x reducer + Off axis MA600

In this configuration, hall effect encoders are used to sense commutation and an MA600 is used in conjuction with a diametrically magnetized ring magnet for output positioning.  It is designed as one of the lowest cost options for a hollow axis actuator with a gear reduction, as the off-axis MA600 has minimally acceptable performance as does the hall effect sensors.

The MA600 is connected to AUX1 on a moteus-n1 [(n1 pinout)](../reference/pinouts.md#moteus-n1) or moteus-x1 [(x1 pinout)](../reference/pinouts.md#moteus-x1) and the hall effect sensors are connected to AUX2.

First, we will configure the hall effect sensors and calibrate them.

```
aux2.pins.0.mode 6  # hall
aux2.pins.0.pull 1  # pull_up
aux2.pins.1.mode 6  # hall
aux2.pins.1.pull 1  # pull_up
aux2.pins.2.mode 6  # hall
aux2.pins.2.pull 1  # pull_up
aux2.hall.enabled 1
motor_position.rotor_to_output_ratio 0.1
motor_position.sources.0.aux_number 2
motor_position.sources.0.type 4  # hall
```

Then, the hall effect sensors are calibrated:

```
python -m moteus.moteus_tool -t 1 --calibrate --cal-motor-poles 30
```

Now we will configure the MA600.

```
aux1.pins.0.mode 1  # spi
aux1.pins.1.mode 1  # spi
aux1.pins.2.mode 1  # spi
aux1.pins.3.mode 2  # spi_cs
aux1.spi.mode 5     # ma600
aux1.spi_rate_hz 6000000
motor_position.sources.1.aux_number 1
motor_position.sources.1.type 1  # spi
motor_position.sources.1.cpr 65536
motor_position.sources.1.reference 1  # output
```

Then, before configuring the MA600 to be used for output, match the sign of the MA600 and hall effects according to [the procedure here](#match).

For an off-axis MA600, BCT tuning should be performed, and non-linear compensation may be performed.

```
moteus$ ./utils/measure_ma732_bct.py
```

To peform non-linear compensation, you can use:

```
moteus$ ./utils/compensate_encoder.py
```

Finally, the MA600 can be configured as the output source:

```
motor_position.output.source 1
```

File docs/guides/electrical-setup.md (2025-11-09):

# Electrical Setup

To use moteus without damage, proper care must be paid to the electrical connections and configuration.  This section describes how.

## Electrical Connections

**Motor**: Phase wires for the motor should be soldered to the pads labeled A, B, and C. The order does not matter. The location of the pads varies between controllers.  An inline connector, like an MR30, MR60, or bullet connectors can be used if repeated disconnection is desired.

**Power**: Power is provided via either the onboard XT30 connector, or on board-mountable moteus controllers, via the power pads that are interleaved with the A, B, and C phase pads.  The power input is *NOT* protected against reverse polarity.  Polarity should be triple checked before applying power, or irreversible damage may result.  XT30 connectors have a clear '+' and '-' marking on them which can be used to identify the positive and negative input.

If you are unsure, pinout diagrams for all controllers can be found here: [Pinout diagrams](../reference/pinouts.md)

!!! note "Hot plugging"
    It is important to *never* hot plug an XT30 connector.  The XT30 connector (and all connectors which are not anti-spark), should be connected *before* power is applied.  If you see or hear a spark, you have applied power in the wrong order.  See the below section on inrush current management.

## Soldering and cable construction techniques

moteus controllers can be damaged when improper techniques are used to attach wires to them, or improper techniques are used to construct power cables.

### Phase Wire Soldering

The connections between moteus and the motor under control must be high quality.  Poor quality solder joints can cause intermittent changes in resistance, sparking, and high voltage transients.  High quality solder joints require:

* Sufficient flux to clean oxides off of the wire and the via
* Sufficient temperature so that the entire wire and via is hot enough for the solder to wet all surfaces

For the former, it is often necessary to add copious amounts of additional flux in addition to the rosin core inside many solders.  For the latter, a high power soldering iron, with a fat tip, and what seems like a long time may be necessary.  The temperature is definitely insufficient if solder touched to any part of the via or wire does not melt and wick instantly.  Usually a small amount of solder is placed between the tip and wire to act as a heat transfer agent.  Then the iron rests on the via and wire for between 5-30s until it looks like the initial solder has wicked fully into the via.  Then additional solder can be added until it forms a clean smooth fillet around the entire via wicking up to the wire.

When complete, the back side of the hole can be examined, and if successful, solder will have wicked partially down out of the via onto the other side forming a clean, smooth fillet there as well.

A demonstration of this can be found in the following video: [https://www.youtube.com/watch?v=mZ9w_TaWmjQ](https://www.youtube.com/watch?v=mZ9w_TaWmjQ)

{{ youtube("mZ9w_TaWmjQ") }}

### Power Cable Construction

When constructing power cables using XT30 connectors, it is critical that solder joints be sound, otherwise intermittent connectivity can result.  This can cause sparking and high voltage transients.  The soldering principles are the same as in the phase wire soldering section above.

A demonstration of XT30 soldering can be found in the following video:
[https://www.youtube.com/watch?v=f6WtDFWuxuQ](https://www.youtube.com/watch?v=f6WtDFWuxuQ)

{{ youtube("f6WtDFWuxuQ") }}

### Power Connectorization

For moteus to operate without damage, the XT30 connectors used to transmit power must make a solid connection that is non-intermittent.  As with poor soldering, an intermittent connection can cause inductive spikes, which will destroy components on the controller.

When connectors are functional, moderate insertion force should be required and the connectors should not "wiggle" much after insertion.

The XT30 is not rated for any significant amount of mechanical force when mated.  For any application where cables may flex, strain relief should be used such that no force is applied to the connector.  The connector may be damaged if a system goes "out of control" even in one instance, although milder mechanical stress may cause accelerated fatigue and failure.

If sparks are observed, that is *definitely* a problem and the system should be powered off until the connectors can be replaced and mitigations made for what led to that event.

Genuine AMASS connectors are rated for 1000 insertions assuming no other mechanical damage, however off-brand connectors may have worse tolerances and may not make a reliable connection for even one insertion.

### Long daisy chains

When connecting more than 3 moteus controllers or servos in a system on a single power or CAN chain, additional factors should be considered.

1. It is recommended to use T-spliced power instead of using the daisy chained power connectors for chains greater than 3 units.  Small connector mis-seating or micro-arcing will cause magnified effects with long chains of controllers.

2. CAN bus electrical performance can be a limiting factor.  To operate at the default 5Mbps, you will need to ensure that CAN wires are twisted, all crimps are high quality, and that termination is installed.  Split termination may be required, where two 60 ohm resistors are connected in series with a small filter capacitor connected between the center tap of the resistors and ground.  A 4.7nF capacitor is recommended.  If that is insufficient, BRS can be disabled to operate only at 1Mbps.  With `moteus_tool` or `tview`, the `--can-disable-brs` flag can be used.

mjbots sells a CAN terminator that can be used for this purpose: [https://mjbots.com/products/jst-ph3-can-fd-terminator](https://mjbots.com/products/jst-ph3-can-fd-terminator)

## Inrush current management

moteus controllers have large DC bulk capacitance with low ESR, this is how they can achieve their small form factor.  As a result, care must be taken when applying power.  If a connector is "hot-plugged" extremely large transient currents can develop which may damage the moteus or other components in the system.  These challenges are magnified when more than one moteus controller is attached to the same power bus.

Potential solutions:

**Power Supply**: If a wall power supply is used, it can be relied upon to provide a "soft start" functionality.  Ensure that all moteus controllers are attached to the power supply *before* enabling the supply by turning it on or plugging it into a wall.

**Anti-spark connectors**: There exist anti-spark connectors like the XT90-S, which have a power resistor built in which makes contact before main power is applied.  These can be used, but have several drawbacks:

1. The proper order of connection must always be obeyed.  Unless the XT90-S is connected *last*, then inrush transients may result.
2. If the power rating on the built-in resistor is not respected, it will silently fail, resulting in no pre-charge protection at all.

**Active pre-charge circuits**: mjbots sells the [mjpower-ss](https://mjbots.com/products/mjpower-ss) and [power_dist](https://mjbots.com/products/mjbots-power-dist-r4-5b), both of which have the primary function of gradually precharging capacitive loads.  Other active pre-charge systems may also be viable.

## Regenerative braking safety

moteus can be commanded to sharply decelerate loads, either directly in response to commands, or due to external disturbances.  When braking a load, moteus by default applies the generated power to the input DC bus.

If there is nowhere for this power to go, this can cause problems.  The voltage can increase without bound, which in mild cases will cause the CAN transceiver on all devices connected to the bus to fail, and in severe cases can explode the main FETs or other components on the board.

Here's what you should know about the facilities moteus has to deal with this, and what you can do to make your design safer.

### Flux braking

The feature within moteus itself to deal with this is "flux braking".  The flux braking implementation will dissipate extra power in the windings of the motor when the bus voltage gets above a certain threshold.  This is controlled by the `servo.flux_brake_margin_voltage` and `servo.flux_brake_resistance_ohm` parameters documented above.

### Design considerations for regenerative braking

The following design considerations can be used to minimize the risk of damage to hardware in the event of overvoltage.  These are not a substitute for validation in progressively more demanding situations, but they can help you start off in a good place.

- *Tightly scope the over-voltage fault / flux braking*: The configuration parameter `servo.max_voltage` can be lowered for all devices on the bus.  This will both cause a fault if the voltage exceeds this value and in conjuction with `servo.flux_brake_margin_voltage`, select the point at which moteus will attempt to dissipate energy to prevent an overvoltage scenario.  It is recommended to set this to no less than 5V above the maximum expected supply voltage.

- *Power from a battery, not a PSU*: When not charged, batteries are capable of sinking current to minimize over-voltage transients.  However, if the battery is fully charged, most battery management systems drastically reduce the allowable charging current.  Thus, a battery is only useful as a mitigation if it is never charged above say 75 or 80% state of charge.

- *Decrease overall system voltage*: If you run the moteus controller with say a 10S battery, the peak input voltage can be as high as 42V.  That does not leave very much margin for regenerative loads.  For applications that experience sharp regenerative loads and do not have a battery capable of charging always attached, it is recommended not to exceed 8S (33.6V peak).

- *Use a supply which can sink as well as source*: Powering from an inexpensive lab supply is the most dangerous, as they typically have no ability to sink current, only source it.  A "two quadrant" supply is the necessary device.

## Next Steps

After completing electrical connections, proceed to [software installation and configuration](software-installation.md) to begin using your moteus controller.

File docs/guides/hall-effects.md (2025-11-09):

# Motor with Hall Effect Sensors

Many motors include hall effect sensors used to provide commutation information to motor controllers.  moteus is able to use hall effect sensors for both commutation and output positioning.  First, some caveats:

**They may not be needed**: Just because a motor has hall effect sensors built in, does not mean you need to use them.  If you can use the on-axis magnetic encoder integrated into moteus by mounting moteus appropriately relative to the rotor, that will always give better results than using hall effect encoders.

**You will likely need additional hardware**: Most configurations with hall effects will require additional filtering capacitors, placed near moteus, between each signal line and ground.  1nF is a recommended starting point.  They can be added either in the wire harness, or on unpopulated 0402 pads on the moteus-c1, moteus-n1, and moteus-x1.

**Hall effect sensors used for output positioning have very poor low velocity performance**: While hall effect sensors are minimally useful for commutation and higher speed output operation, they will provide poor performance when used as an output encoder at low speeds.  That means many position control applications, which are inherently often at low speed, will give poor results.

**moteus-r4 cannot easily drive many hall effect sensors**: moteus-r4 specifically has only 3.3V supply for external devices, whereas most hall effect encoders require 5V.  Further, the only means of connecting hall effect sensors to moteus-r4 are using unpopulated pads on the back of the board, and *not* using the onboard encoder.  Other moteus products do not have these specification limitations regarding supply voltage and connectors.

If using hall effects for commutation or output positioning is still desired, the below configurations can get you started.

## aux2 configuration ##

This configuration uses hall effect sensors connected to the aux2 GH7
connector for both commutation and output positioning.

moteus-c1 [(c1 pinout)](../reference/pinouts.md#moteus-c1), moteus-n1 [(n1 pinout)](../reference/pinouts.md#moteus-n1), and moteus-x1 [(x1 pinout)](../reference/pinouts.md#moteus-x1) all have an aux2 GH7 connector that can provide 5V output and has 5V tolerant IO pins.  The typical wiring diagram looks like the below, although the hall connector is "nominal" as there is no real standard:



As mentioned above, either 1nF capacitors should be installed in the harness between each signal line and ground, or installed on the appropriate unpopulated pads on the board.

The following aux2 configuration parameters should be set.

```
aux2.pins.0.mode 6  # hall
aux2.pins.0.pull 1  # pull_up
aux2.pins.1.mode 6  # hall
aux2.pins.1.pull 1  # pull_up
aux2.pins.2.mode 6  # hall
aux2.pins.2.pull 1  # pull_up
aux2.hall.enabled 1
```

Then motor_position is configured as follows:

```
motor_position.sources.0.aux_number 2
motor_position.sources.0.type 4  # hall
```

Finally, when calibrating, the number of poles is required to be
specified.

```
python -m moteus.moteus_tool -t 1 --calibrate --cal-motor-poles 30
```

## Advanced: Dual Encoder Setup

A more performant configuration may use the hall effect sensors for commutation and a different encoder measuring the output position.  That is not directly described here, but you can look at the [Dual Encoders](dual-encoders.md) guide as well as the [encoder reference](../reference/encoders.md) to understand how to configure it.

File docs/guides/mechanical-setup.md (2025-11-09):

# Mechanical Setup

To use the onboard on-axis encoder integrated with moteus, the controller must be mounted with care to ensure proper alignment and ongoing registration.

## Mechanical Mounting

If using the default onboard encoder, the following steps must be taken:

1. A diametrically magnetized sense magnet should be attached to the rotor. The fastening must be rigid, allowing no slip. Adhesive is generally required, cyanoacrylate or epoxy can be used.
2. The moteus controller must be mounted so that the encoder is (a) centered laterally on the sense magnet and (b) has an air-gap of approximately 2mm. This mount must be rigid and allow no slip.

!!! note "moteus-r4 mounting"
    Unlike other moteus controllers, the moteus-r4 encoder is *not* centered under the bolt pattern, check the [2D CAD for details](https://github.com/mjbots/moteus/blob/main/hw/controller/r4.5/20210124-moteus-controller-r45-mechanical.pdf).

!!! note "3D printed mounts"
    If using 3D printed mounts, care should be taken to ensure the mount does not warp.  PLA and other low temperature filaments will warp under load at room temperature, and will do so even more when exposed to thermal heating like from a motor controller.  It is recommended to use PETG, PC, or a filament designed to not warp at the operating temperature you intend.

## Additional Considerations

There are additional considerations when mounting, some mostly common sense, and some unique to moteus.

### Protection from debris and stray conductors

It is advisable to mechanically shield moteus controllers from the environment during operation to prevent contact with stray conductors, dirt, or debris.  Contact with any of these things while the system is energized can result in failure.

Similarly, manipulating or working on the system while it is energized should be avoided.

### moteus-n1 light sensitivity

moteus-n1 has a voltage regulator which is light sensitive and will fail when exposed to sunlight.  The enclosure used to house the system should be opaque.  If for some reason an enclosure can not be used, opaque expoxy can be placed over the voltage regulator IC.

moteus-c1, moteus-r4 and moteus-x1 have no light sensitivity considerations to take into account.

## Next Steps

Once mechanical mounting is complete, proceed to [Electrical Setup](electrical-setup.md) to connect the motor phase wires and power.

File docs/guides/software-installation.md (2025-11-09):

# Software Installation

This guide covers installing the software tools needed to communicate with and configure your moteus controller.

## Installing moteus_gui

The moteus_gui package provides essential tools including `tview` (telemetry viewer) and `moteus_tool` (configuration utility). Installation varies slightly by platform.

=== "Linux"

    ```bash
    python -m pip install moteus-gui
    ```

    **Note**: On Linux, you may need to use either a [virtual environment](https://docs.python.org/3/library/venv.html#creating-virtual-environments) or the `--break-system-packages` option.

    **fdcanusb udev rules**: If using the fdcanusb or mjcanfd-usb-1x adapter, you may need to set up udev rules so regular users can access the device. Follow the instructions at: [https://github.com/mjbots/fdcanusb/blob/master/70-fdcanusb.rules](https://github.com/mjbots/fdcanusb/blob/master/70-fdcanusb.rules)

=== "Windows"

    ```bash
    python -m pip install moteus-gui
    ```

    **Note**: On some older Windows installations, you need to invoke python as `python3`, not `python`.

=== "macOS"

    ```bash
    python -m pip install moteus-gui
    ```

=== "Raspberry Pi (cmdline only)"

    ```bash
    python -m venv moteus-venv --system-site-packages
    ./moteus-venv/bin/pip install moteus

    ```

    **Note**: For complete Raspberry Pi setup instructions including GUI and hardware configuration, see [Raspberry Pi Setup](../platforms/raspberry-pi.md).

## Running tview

tview is the primary tool for configuring and inspecting the state of your moteus controller. Launch it with:

```bash
python3 -m moteus_gui.tview
```

**Alternative**: Your pip installation may have added a `tview` script to your PATH, which you can use instead.

## Understanding tview

tview has three main panes: left, right, and bottom.



### Left Pane Tabs

The left pane contains two tabs:

**Right tab (default)**: Shows a hierarchical tree of all telemetry items currently being reported by the controller.

**Left tab**: Shows a hierarchical tree of all configurable parameters. You can update parameter values by double-clicking on their value and entering a new one.

### Right Pane

The right pane displays real-time plots of telemetry items. You can populate it with plots by right-clicking on telemetry items in the telemetry tab (left pane, right tab).

### Bottom Pane

The bottom pane contains two tabs:

**Left tab - console (default)**: a command line console showing the moteus diagnostic protocol.  It:

- Shows commands sent internally by tview and their responses
- Provides an interactive console to interact with the device using the [diagnostic protocol](../protocol/diagnostic.md)

**Right tab - Python**: A python REPL that can be used to interact with the the controller(s) using the moteus python library.

## Next Steps

Now that you have the software installed and understand the tview interface, proceed to the [Configuration](configuration.md) guide to set up your moteus controller for your specific motor and application.

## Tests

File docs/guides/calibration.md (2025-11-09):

# Calibration

If you started from a bare moteus board, you will need to calibrate it for the attached motor before any control modes are possible. Calibration is required when:

- Using a new bare moteus controller for the first time
- Changing to a different motor
- Altering the mechanical registration between the controller and motor
- After certain configuration changes that affect motor characteristics

Development kits typically come pre-calibrated and do not require this step unless the motor is changed.

## Calibration Command

To calibrate your moteus controller, run the following command:

```bash
python3 -m moteus.moteus_tool --target 1 --calibrate
```

Replace `1` with the appropriate CAN-FD ID if you have configured your controller to use a different ID.

## Important Safety Warning

**WARNING: Any attached motor must be able to spin freely during calibration.**

During the calibration process:

- The motor will be spun in both directions
- The motor will reach high speeds
- Ensure no mechanical obstructions are present
- Do not apply any load to the motor shaft
- Keep hands and objects clear of the motor and any attached mechanisms

The calibration procedure measures motor electrical characteristics and encoder alignment, which requires unrestricted motor motion.

## Alternate calibration parameters

### Limited rotation

The amount of motion required for calibration can be reduced if the Kv of the motor is known in advance.  In that case, specify as an additional command line argument:

`--cal-force-kv X`

Where X is the Kv of the motor.  In this mode, moteus will only spin the rotor 360 degrees in each direction and will not perform a high speed movement.

### Very small or very large motors

During the encoder calibration process, moteus applies a constant power to the motor.  The default power, 7.5W is sufficient for many motors but not all.  If the motor is very small, it could overheat or burn if applying that much power.  If the motor is very large, 7.5W may not be enough to cause the motor to move.  This can be altered by specifying:

`--cal-motor-power X`

Where X is the power in watts to apply.  Small motors will need smaller values, large motors may need larger ones.

### Updating encoder and torque bandwidth

If your application requires changing torque or velocity very quickly, you may want to configure an alternate "bandwidth" parameter during the calibration process.  The specific value of bandwidth can be roughly used to estimate how quickly moteus can change the output torque, and how quickly it can sense velocity and position changes.  For instance, the default bandwidth is 200Hz.  This means that as a rough order of magnitude, moteus can change the torque or observe a change in velocity in 1/200 = 5ms.  Higher bandwidth values will result in the controller and motor emitting more audible noise.  Other than audible noise (which can be significant), there is not much downside to increasing the bandwidth.

`--cal-bw-hz X`

## Troubleshooting

If you encounter issues during calibration, such as:

- Motor not spinning
- Calibration failures or errors
- Unexpected motor behavior

Refer to the [Troubleshooting Guide](../troubleshooting/calibration.md) for common problems and solutions.

## Next Steps

After successful calibration, you can conduct the PID tuning process:

- [PID Tuning](../guides/pid-tuning.md)

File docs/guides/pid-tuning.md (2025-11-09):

# PID Tuning

When operating in position or velocity mode, moteus uses a P(I)D controller to determine what torque to apply at each instant.  The constants that control this operation need to be selected by the user.  Tuning does not have to be challenging, but does require that you understand what you are trying to accomplish.

## Theory

The purpose of the three gains:

**Proportional**: This term applies a restorative torque that is proportional to the error between the current desired position and the current measured position.  It is measured in Nm per revolution of error as measured at the output of the reducer.  It directly controls the "stiffness" of the controller.  If used in isolation, the motor will apply a fixed torque for any given error, i.e. if you manually move the motor 0.1 revolution away from the setpoint, it will apply 0.1 * the torque indefinitely, and then if you move it to be 0.2 revolution away from the setpoint, it will apply 0.2 * the torque.

**Derivative**: This term acts as a "damping" term, or viscious resistance.  As an analogy, if the proportional term is the spring in a suspension system, the derivative term is how thick the oil in the suspension is.  The torque applied from this term scales with the magnitude of the error between the desired velocity and the measured velocity.  If all other gains were zero and the motor is disturbed by hand, a larger gain makes it feel like you are working against a thicker fluid resistance.

**Integrative**:  The integrative term applies a torque that scales with the error in position integrated over time.  Many, if not most, moteus systems use no integrative term at all.  Integrative terms are hard to tune, and result in poor transient response.  However, they are the only way to achieve 0 steady state error in a loaded system.  Without an integrative term, the steady state error, while possibly very small, will never be zero.  For the integrative term there are two parameters to select, the gain itself, and the anti-windup gain term.

## Procedure

The position control P(I)D loop parameters are set in `servo.pid_position` and are selected by the user to achieve a desired control response.  Most users want a PID controller that is well damped and sufficiently stiff for their application.

Here is a possible procedure for tuning.  It is best executed using tview in a configuration where you can move the rotor with your hand.

1. Set kp to be small and kd, ki, and ilimit to be 0.
```
servo.pid_position.kp = 0.001
servo.pid_position.kd = 0
servo.pid_position.ki = 0
servo.pid_position.ilimit = 0
```
If you have an understanding of the system, you could select an initial kp that is larger, but you want it to be a value such that the restorative torque is very gradual and you can easily disturb the system by hand.
2. Increase kp by 50% at a time until the desired stiffness is reached.
    1. Test the current value.  A command like `d pos nan 0 nan` can be used to "hold position".  Then use your hand to move the rotor to judge the stiffness.
    2. If insufficiently stiff, increase `servo.pid_position.kp` by 50% and go back to (a)
    3. If vibration or instability results, decrease `servo.pid_position.kp` by 2x and that is roughly a good stable maximum.
3. Tune the derivative term
    1. Set kd initially to 1/100th of the kp value. For example, the following where FOO is 0.01 * the selected value for `servo.pid_position.kp`.
`servo.pid_position.kd = FOO`
    2. Test the current value.  Use `d pos nan 0 nan` to hold position.  Manually move the motor away from the setpoint, then quickly release it.  If "damped" the motor will smoothly come to a stop at the original position.  If underdamped, the motor may oscillate.
    3. If insufficiently damped, increase `servo.pid_position.kd` by 50% and go back to (a)
    4. If high frequency vibration or oscillation results, decrease `servo.pid_position.kd` by 2x and that is roughly a good stable maximum.
4. If zero steady state error is required, then an integrative term is required.  If not, leave `ilimit` at 0 and you are done.
5. Configure the integrative term.
    1. Set `servo.pid_position.ilimit` to be 20% higher than the maximum expected steady state torque.
    2. Set an initial value of `servo.pid_position.ki` equal to the `servo.pid_position.kp` term.
    3. Increase `servo.pid_position.ki` until the desired response is achieved.  `ki` will likely need to be numerically much larger than kp, on the order of 10-1000x larger.  A more representative control profile than just a "hold position" may be needed to determine if the selected integrative constants are sufficient.

## Acceleration limited trajectories

Further, it is *strongly* recommended to configure and use an acceleration limit with moteus that is physically achievable in your system.  Doing so means that the "desired" position and "desired" velocity will follow continuous, physically achievable trajectories.

- `servo.default_accel_limit` can be set in Hz / s.

If you do not set an acceleration limit, or select one that is too high to be physically achievable, your system will experience overshoot during movements and you will find it challenging to tune the P(I)D parameters to achieve a desired response.

## What not to tune

The "current loop" gains are set in `servo.pid_dq`, and are set during
calibration based on the desired torque bandwidth.  They are not
normally changed by the user.  Instead, they are selected by specifying an appropriate `--cal-bw-hz` during calibration.

## Next steps

Now you are ready to control moteus using one of the possible control modes:

- [Control](../guides/control-modes.md)

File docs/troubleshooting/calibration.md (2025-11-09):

# Troubleshooting Calibration

When setting up a [moteus controller](https://mjbots.com) with a new motor, you typically first run the automatic calibration sequence as [documented in the reference manual](../guides/calibration.md). When your system is working well, that should be all that is necessary to enable moteus to perform accurate FOC based torque control of the motor. Then you can continue on with the remainder of the items in the [Quick Start](../quick-start.md). What happens though when the automatic calibration doesn't work? This article describes the most common failure modes during calibration.

Unfortunately, most calibration failures present the same final symptom, an error like:

```
CAL timeout
```

or

```
encoder not an integral multiple of phase
```

So to resolve, you typically start with the first items in this article, then work your way down to the less common ones.

## Sense magnet issues

To operate properly using the onboard encoder, moteus requires that a diametrically magnetized sense magnet be rigidly affixed to the rotor, that it be centered laterally under the magnetic encoder on moteus, and that it has an appropriate air-gap. Let's look at each of those in turn.

First, you need a [diametrically magnetized magnet](https://www.kjmagnetics.com/magdir.asp). This is one where the axis of magnetization is sideways, so that the north pole points out of the curved side of the disc. This is contrast to axially magnetized magnets where the axis of magnetization points out of the flat side. There are a wide variety of possible options here. Every moteus controller sold at [mjbots.com](https://mjbots.com) includes an appropriate magnet, and [mjbots.com also sells spares](https://mjbots.com/products/d42dia). There are also suppliers with higher temperature magnets, like the [Radial Magnets, Inc. 9049 here at digikey](https://www.digikey.com/en/products/detail/radial-magnets-inc/9049/6030786). Sometimes however, you are converting an existing actuator to use moteus, and there is a sense magnet present already. The bad news is that it may or may not be usable with moteus and unless you know the specifications, it may be hard to know the optimal air gap required for it. In those cases it is often easiest to remove the existing magnet and replace it with a known quantity, especially if a reasonable air gap is hard to achieve.

Second, the magnet must be rigidly affixed to the rotor. No slipping is permitted whatsoever. Practically, that means that adhesive will be required at each junction between the magnet and the rotor. Common adhesives used are cyanoacrylate gel (superglue), and epoxy. For instance, if a 3D printed spacer is used, the magnet must be glued to the spacer, and the spacer must be glued to the rotor. When the rotor moves, the magnet must move. Press fits can be problematic unless the fit is designed with a well specified tolerance and relying on friction between a magnet and something it is attracted to will definitely not work.

Third, the magnet must be positioned laterally properly. This means that it needs to be centered under the magnetic encoder. For [moteus-n1](https://mjbots.com/products/moteus-n1) and [moteus-c1](https://mjbots.com/products/moteus-c1), that is centered under the bolt pattern. For [moteus-r4](https://mjbots.com/products/moteus-r4-11), you should [look at the 2D CAD](https://github.com/mjbots/moteus/blob/main/hw/controller/r4.5/20210124-moteus-controller-r45-mechanical.pdf) to see where to position the magnet.

The magnet also needs an appropriate air gap between the surface of the magnet and the surface of the encoder IC. For the magnets that mjbots sells, 2mm is near the optimal air gap, with a range of 1.5mm - 2.5mm being suitable. Spacing of 0.5mm - 8mm will likely work with degraded performance.

Finally, the controller needs itself to be rigidly mounted with respect to the stator and rotor. If it is allowed to move or rotate, then the sensed angle of the rotor will not match the actual electrical angle needed for commutation, as well as degrading the quality of position control at the output.

## Electrical problems

The most common electrical problem that prevents calibration is poor or non-existent phase wire soldering. The phase wires of the motor must make a good connection to the moteus phase terminals. That means that when soldering, the joint must have reached a sufficient temperature and had sufficient flux such that the solder wicked both all around the wire, and wicked in to the phase wire terminal. Cold solder joints may show solder that does not fill the joint completely and does not form a proper fillet to the surfaces it touches or may show as visual artifacts between the wire, pad, and solder. This may result in no or an intermittent connection. A video showing what an appropriate result should look like is here:

{{ youtube("mZ9w_TaWmjQ") }}

The next most common electrical problem is a motor that is fundamentally broken. That could be one which has shorted phases, inappropriate polarity of windings, or magnets with inappropriate polarity. These problems usually only appear with second hand motors, those of low quality, or hand-built motors. The easiest way to rule it out is to test with a known working motor.

## Less Common Sense Magnet Issues

I have observed a few less common problems associated with sense magnets.

In one case, the magnet was actually glued both to the rotor and to a stationary mounting bracket, preventing the rotor from moving at all.

In other cases, magnets were allowed to exceed their rated operating temperature. The magnets mjbots sells as of May 2024 are rated to 80C. If the temperature approaches that point, often above 70C, then the axis of magnetization can drift. If that is an issue, then magnets can be procured with higher rated temperatures.

Sense magnets for commutation must be rigidly affixed to the rotor, \*not\* to the output of a reducer, or any linkage that may have backlash. If the magnet is attached to a reducer, then the required angular accuracy can easily exceed what the onboard encoder is capable of measuring. Linkages with backlash have the same problem.

## Mechanical Problems

If your rotor is not free to move, or has a significant load on it, then calibration can fail. Calibration will work with many kinds of reducers attached, but eventually the friction and stiction will be more than the process can manage. In some cases you can increase the power used during the lock-in phase of calibration by passing an extra option to `moteus_tool --calibrate`:

```
--cal-motor-power 5
```

The units are watts, and 5 is the default. You can increase this, but at higher values, you may run the risk of overheating your motor during the encoder calibration process.

If a suitable power cannot be found, then it may be required to design the motor and controller as a sub-assembly which can be first calibrated and then attached to the reducer.

## The bad news

The bad news is that the error checking in the calibration process is not foolproof. i.e. it is possible for a setup that is broken to still report that calibration completed successfully. The two biggest indicators that it did not actually work are that the Kv value reported during calibration is grossly incorrect or that position or torque control do not work reliably. If either of those happen, you need to work through the above potential causes and rule them out one by one.

## The good news

The good news is that if you have a working motor, an appropriate magnet, the magnet is rigidly affixed to the rotor and positioned properly, and your phase wire soldering followed proper technique, calibration should succeed virtually 100% of the time.

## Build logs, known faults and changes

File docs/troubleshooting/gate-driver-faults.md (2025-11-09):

# Troubleshooting Gate Driver Faults

Certain types of electrical problems in moteus can result in the onboard MOSFET gate drivers declaring an error condition.  When that happens, moteus will report fault 33.  This document describes how to troubleshoot the issue.

## Identifying the cause

To determine *which* fault the gate driver flagged, you need to look at the `drv8323` tree in tview or with `python -m moteus.moteus_tool -t 1 --read drv8323`.  Each fault has a different boolean value associated with it, and multiple can be flagged at the same time.  From a diagnostic perspective though, they boil down into two categories:

## Recoverable faults

The only fault type that, if repeatable, is easily recoverable is the `uvlo=true` fault.  This means that the gate driver identified the input supply voltage dropped below the minimum operation threshold.  It happens when moteus attempts to draw more power than the supply or battery can provide.  Depending upon the cause, there are several potential resolutions:

**moteus needs to output more torque/power**: If the fault triggered but moteus was not yet applying sufficient torque for your application, then you must change your supply to be able to provide more power.  If the supply is a current limited lab supply, you could increase the current limit.  If it is a fixed current wall supply, you could switch to one with a higher power output.  If it is a battery, you could switch to one with a higher peak current rating.  It is also possible to occur due to poor supply wiring, i.e. if the resistance of the supply power cables is too high.

**moteus should not attempt to draw that much power**: If moteus was attempting to apply more torque or power than is desirable, there are two limits which can be adjusted.

1. `servo.max_current_A` - This will determine the maximum phase current moteus can output and will correspond to the maximum amount of torque it can output.  This does not directly correlate with supply power, as the supply power required also scales linearly with the motor velocity.  However, it is good to ensure this is not set larger than it needs to be.
2. `servo.max_power_W` - This will determine the maximum amount of power moteus can output to the motor, and thus roughly the amount of supply power it can consume.  If using a power supply with known voltage and current capability, you can set this to be some fraction of that power to leave sufficient margin.

## Unrecoverable faults

Most non-uvlo faults the gate driver reports indicate that the controller has suffered electrical damage.  Most of the reasons are laid out in the electrical section of the user guide:

- [Using moteus: Electrical](../guides/electrical-setup.md)

i.e. poor wire construction can result in micro-arcing which further causes large voltage transients either at the supply terminals, or the motor phase terminals.  Lack of inrush current management also results in large voltage transients at the supply terminals.  Poor strain relief of XT30 connectors, once again, can cause micro-arcing and large voltage transients.

In these cases, it may be possible to recover the controller by replacing components, but doing so requires moderate to advanced SMT rework capabilities that are beyond most users.  Usually the appropriate action is to identify which of the electrical installation guidelines were not adhered to, address them, then replace the controller with a new one.

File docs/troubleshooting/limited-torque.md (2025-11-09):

# Troubleshooting Limited Torque

If moteus is able to control a motor, but is unable produce sufficient torque for your application's needs, this post describes diagnostic steps.

## Outline

There are a few main classes of things that can limit torque.

1. **Misconfiguration**:  Things that fall into this category include PID constants that are not tuned or an overly aggressive current limit or thermal limit.
2. **Under-cooled controller or motor**: If the controller and motor are properly sized for the application, they may still require thermal management to achieve those goals.
3. **Under-sized controller or motor**: If thermal management alone is insufficient, or is not practical, then either a larger controller or larger motor may be required.
4. **Insufficient supply voltage**: With low-Kv motors, it is possible for supply voltage to be a limiting factor.

## Diagnosing

First you need to understand which of the above three classes you are in.  To do so, there are some possible diagnostics and other things to check.

### Output Limit Reasons

As of firmware version 2025-07-21, the firmware will report if a factor is limiting the output current via the "fault" register while in position mode.  The set of possible values are:

- **96 max_velocity**: Maximum velocity: If the observed velocity exceeds the configured maximum velocity, torque is limited in the direction that would cause the velocity to increase.  This is configured with `servo.max_velocity`.
- **97 max_power**: Maximum power: The total power of the output is limited through a combination of a board power profile and `servo.max_power_W`.  [See this post for more](https://blog.mjbots.com/2025/03/29/moaar-power/).
- **98 BEMF**: Maximum system voltage: The supply voltage, combined with the back EMF of the motor and the phase resistance does not permit more current to be applied.
- **99 max_current**: Maximum current: There is a system wide maximum output phase current that is configured in `servo.max_current_A`.
- **100 fault_temperature**:  Temperature: The onboard FET temperature sensor can limit the output current.  This threshold is set in the current firmware with `servo.fault_temperature`/`servo.temperature_margin`.
- **101 motor_temperature**: Temperature: The motor temperature sensor can also limit the output current.  This is configured in `servo.motor_fault_temperature`/`servo.motor_temperature_margin`.
- **102 max_torque**: Maximum torque: With each position mode command, the client can specify a maximum torque to use.  If the combination of the onboard PID and commanded feedforward torque exceeds this, then limiting occurs.
- **103 position_bounds**: Position bounds: If the current position is outside of `servopos.position_min` and `servopos.position_max`, then torque is limited in the direction that would push the motor further outside the bounds.

### Other possibilities

If none of the above limiting flags are present, then the remaining options include:

#### Not stiff enough PID tuning

The torque applied by moteus (aside from any feedforward torque), is determined by the error between the desired and measured position and the error between the desired and measured velocity.  If the constants controlling this process are too low, then moteus will apply very little torque even for large errors.

One common way this occurs with moteus is:

1. A PID tuning is created
2. Later, a reducer is configured using `motor_position.rotor_to_output_ratio`
3. Wow, now moteus doesn't output much torque

The important point to note here is that the PID terms for the moteus control loop are measured at the *output* of any reducer.  Thus if kp=1, that means apply 1Nm of torque *at the output* for 1 revolution of error *at the output*.  With a reducer, that means the effective gains at the rotor are reduced by the reduction squared.

So, after configuring a reducer, you can either re-tune the PID gains, or increase the gains by the square of the reduction.

Sample:

```
servo.pid_position.kp = 4
servo.pid_position.kd = 0.05
motor_position.rotor_to_output_ratio = 1
```

You test this and it works great.  Then you configure the 8x reducer which was always present.

```
motor_position.rotor_to_output_ratio = 0.125
```

And now all of a sudden the controller barely does anything at all.
To have equivalent stiffness, you now need to increase the kp and kd
gains by a factor of `8 ** 2 = 64`.

```
servo.pid_position.kp = 256
servo.pid_position.kd = 3.2
```

#### Invalidated calibration

If your calibration was invalidated, it can result in lack of torque.  Invalidation can happen for any of the reasons in the [calibration troubleshooting guide](calibration.md), and include:

- A sense magnet that was not rigidly affixed to the rotor, say because adhesive not used at a joint
- A sense magnet that exceeded its rated temperature
- The controller mounting shifted

To test these hypotheses, re-calibrate the motor and check again.  If
the problem is resolved, then you need to identify which of the above
issues was the most likely culprit and resolve it.

#### Other "limiting like things"

There are some "limiting-like" features that do not report through the
fault code mechanism.  If position bounds are configured, the control
position is limited to stay within those bounds.  This does not
directly limit torque, so is not reported via this mechanism.

Similarly, if the commanded velocity exceeds either the velocity
limit, `velocity.max_velocity`, or `servo_stats.motor_max_velocity`,
then it is truncated to stay within.  These limits are not reported
via the fault code mechanism.

## Resolution

If the error was mis-configuration, fix it and you are done.

If the error was not mis-configuration, then the resolution depends upon what was causing the limiting.

### Thermal limiting

If the limit was thermal, then your options are:

1. apply cooling to whatever was hot
2. use a bigger controller or motor for whatever was hot
3. use a reducer, or if already using a reducer, use a bigger one

### Maximum current

If you hit the controller maximum current limit, then your options are:

1. use a different motor
2. use a controller with a higher current limit
3. use a reducer, or if already using a reducer, use a bigger one

### BEMF or `servo_stats.motor_max_velocity`

If you are limited by the back EMF of your motor, then your options are:

1. use a higher supply voltage
2. use a different motor with a higher Kv rating

### max power

Here, your options are:

1. configure a higher PWM frequency
2. use a bigger controller
3. use a different motor
4. use a reducer, or if already using a reducer, use a bigger one

## Resolution caveats

### Reducers

If considering using a reducer or a bigger reducer, the biggest caveat is that the maximum speed will be decreased by a corresponding amount.

Secondarily, most reducers have backlash and will add static and dynamic friction to your system and may have limits on maximum torque or speed that become limiters.

### PWM frequency

If increasing the PWM frequency to improve peak power, this will also decrease the efficiency of moteus.  That will result in lower continuous output current and power ratings.

### Cooling

The obvious downsides of cooling are noise, lower reliability, and increased power consumption even when under no load.

## moteus performance analysis tool

If attempting to design a motor system to achieve a particular goal, it may be useful to use the moteus performance analysis too, which lets you vary these parameters and measure the resulting performance of the system.

- [https://mjbots.github.io/moteus/mpat.html](https://mjbots.github.io/moteus/mpat.html)
- [mpat blog post](https://blog.mjbots.com/2025/07/17/moteus-performance-analysis-tool-v2/)

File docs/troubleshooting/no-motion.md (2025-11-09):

# Troubleshooting No Motion

You sent a command to moteus, or ran a script, but nothing moved.  This article will describe what steps you can take to diagnose and resolve the issue.

## Using tview

If you sent a `d pos` command from tview, there are a few possibilities.

**Invalid Syntax**: If the diagnostic channel responds with an OK, then this is not the problem.  If it responds otherwise, then the error message will give you a clue as to the problem.  The syntax for the `d pos` command can be found in the [diagnostic protocol reference manual]( http://localhost:8000/mjbots/moteus/protocol/diagnostic/#d-pos).

**Position Mode Fault**: If the diagnostic channel responded OK, then to identify the problem you must look at the current reported mode and fault status.  They will be present as the first two items in the `servo_stats` telemetry channel.  Common problems when first attempting control are:

 - "39 (outside bounds)": `servopos.position_min` and `servopos.position_max` are either not configured, or the motor starting position is outside the configured bounds.  Setting either to `nan` will disable it.
 - "33 (gate driver fault)": this indicates that the onboard MOSFET gate driver reported a fault.  To know which one, you will need to expand the `drv8323` telemetry channel.  The only "easy" problem to solve is `uvlo` which indicates that moteus attempted to draw more power than your supply could provide.

Once the cause of the fault has been identified, it can be cleared by sending:

`d pos`

Then the command in question can be attempted again.

## From a script or application

If you have a python script, C++ application, or other tool which is commanding moteus and it does not move, there are a few tools you can use.

**Request and display the mode and fault**: If your application does not already request and display the mode and fault it should do so.

**Log CAN-FD data**: If the application cannot be modified or it is difficult to do so, you can either (a) if it is using the python library use the `--can-debug OUT.LOG` command flag to save a record of all frames sent and received or (b) attach a second CAN-FD adapter to the bus and use it to log data.

Once you have data, it can be examined using `utils/decode_can_frame.py` to see what moteus is reporting.

Problems may be the same as from the "Using tview" section above.

Another common problem with applications using the register protocol (what the python and C++ library does), is watchdog timeouts.  For the register protocol, by default, moteus requires commands arrive at least every 100ms or it will enter mode 11, the timeout mode.  Once in this mode, a "stop" command must be sent to clear it.

The watchdog timer configuration is described in [the reference manual](../reference/configuration.md#servodefault_timeout_s).

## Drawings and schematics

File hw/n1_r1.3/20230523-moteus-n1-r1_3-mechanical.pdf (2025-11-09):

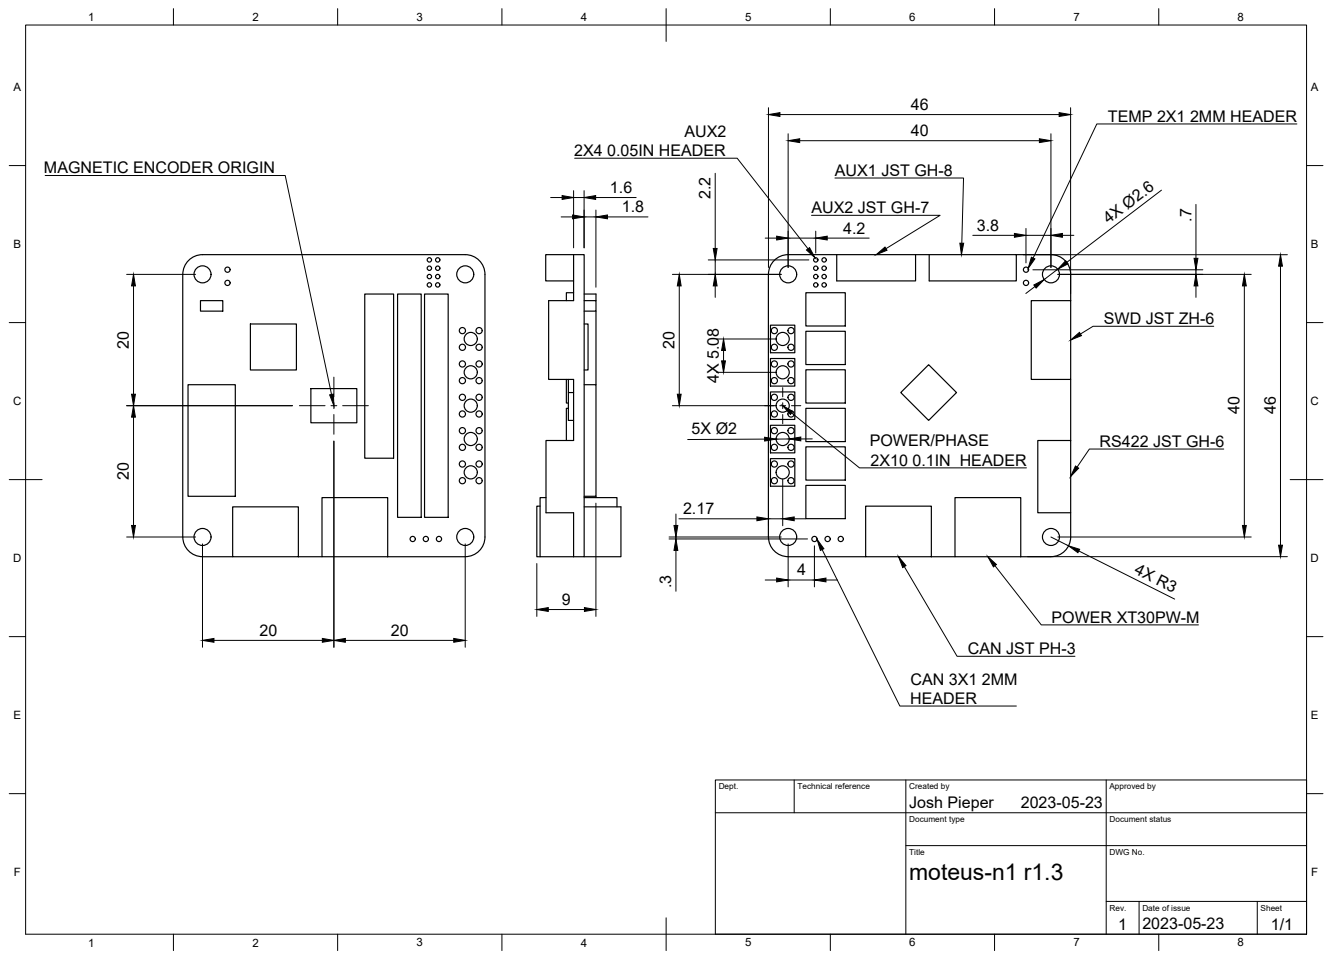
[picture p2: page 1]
Title; DWG No.; Rev.; Date of issue; Sheet; moteus-n1 r1.3; POWER XT30PW-M; AUX2 JST GH-7; AUX1 JST GH-8; RS422 JST GH-6 4X 5.08 20; POWER/PHASE; 2X10 0.1IN HEADER; 2X4 0.05IN HEADER .3; CAN 3X1 2MM; TEMP 2X1 2MM HEADER

MAGNETIC ENCODER ORIGIN

SWD JST ZH-6

CAN JST PH-3

Dept. | Technical reference | Created by Josh Pieper 2023-05-23 | Approved by

Document type | Document status

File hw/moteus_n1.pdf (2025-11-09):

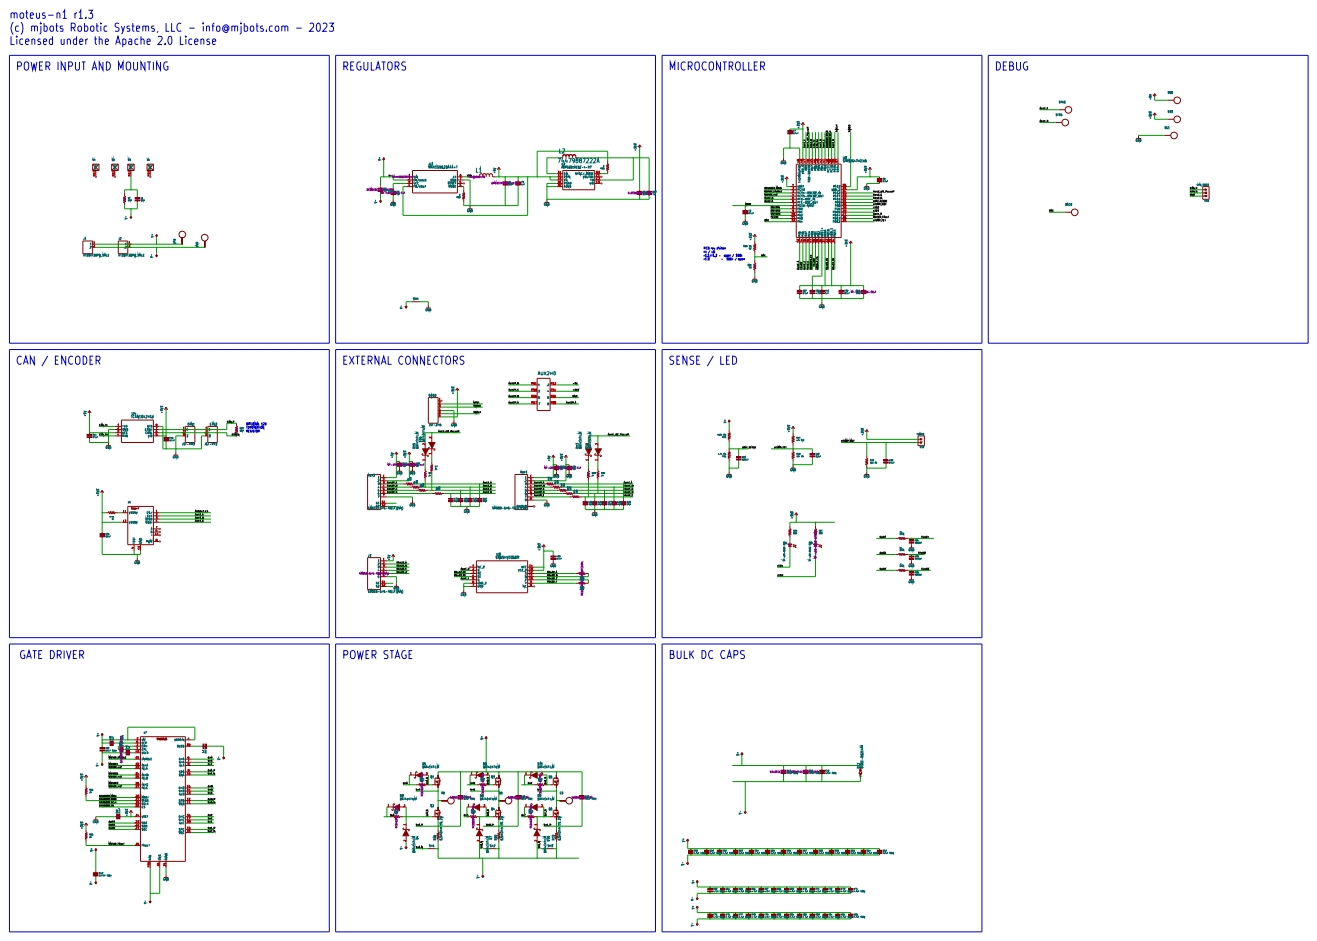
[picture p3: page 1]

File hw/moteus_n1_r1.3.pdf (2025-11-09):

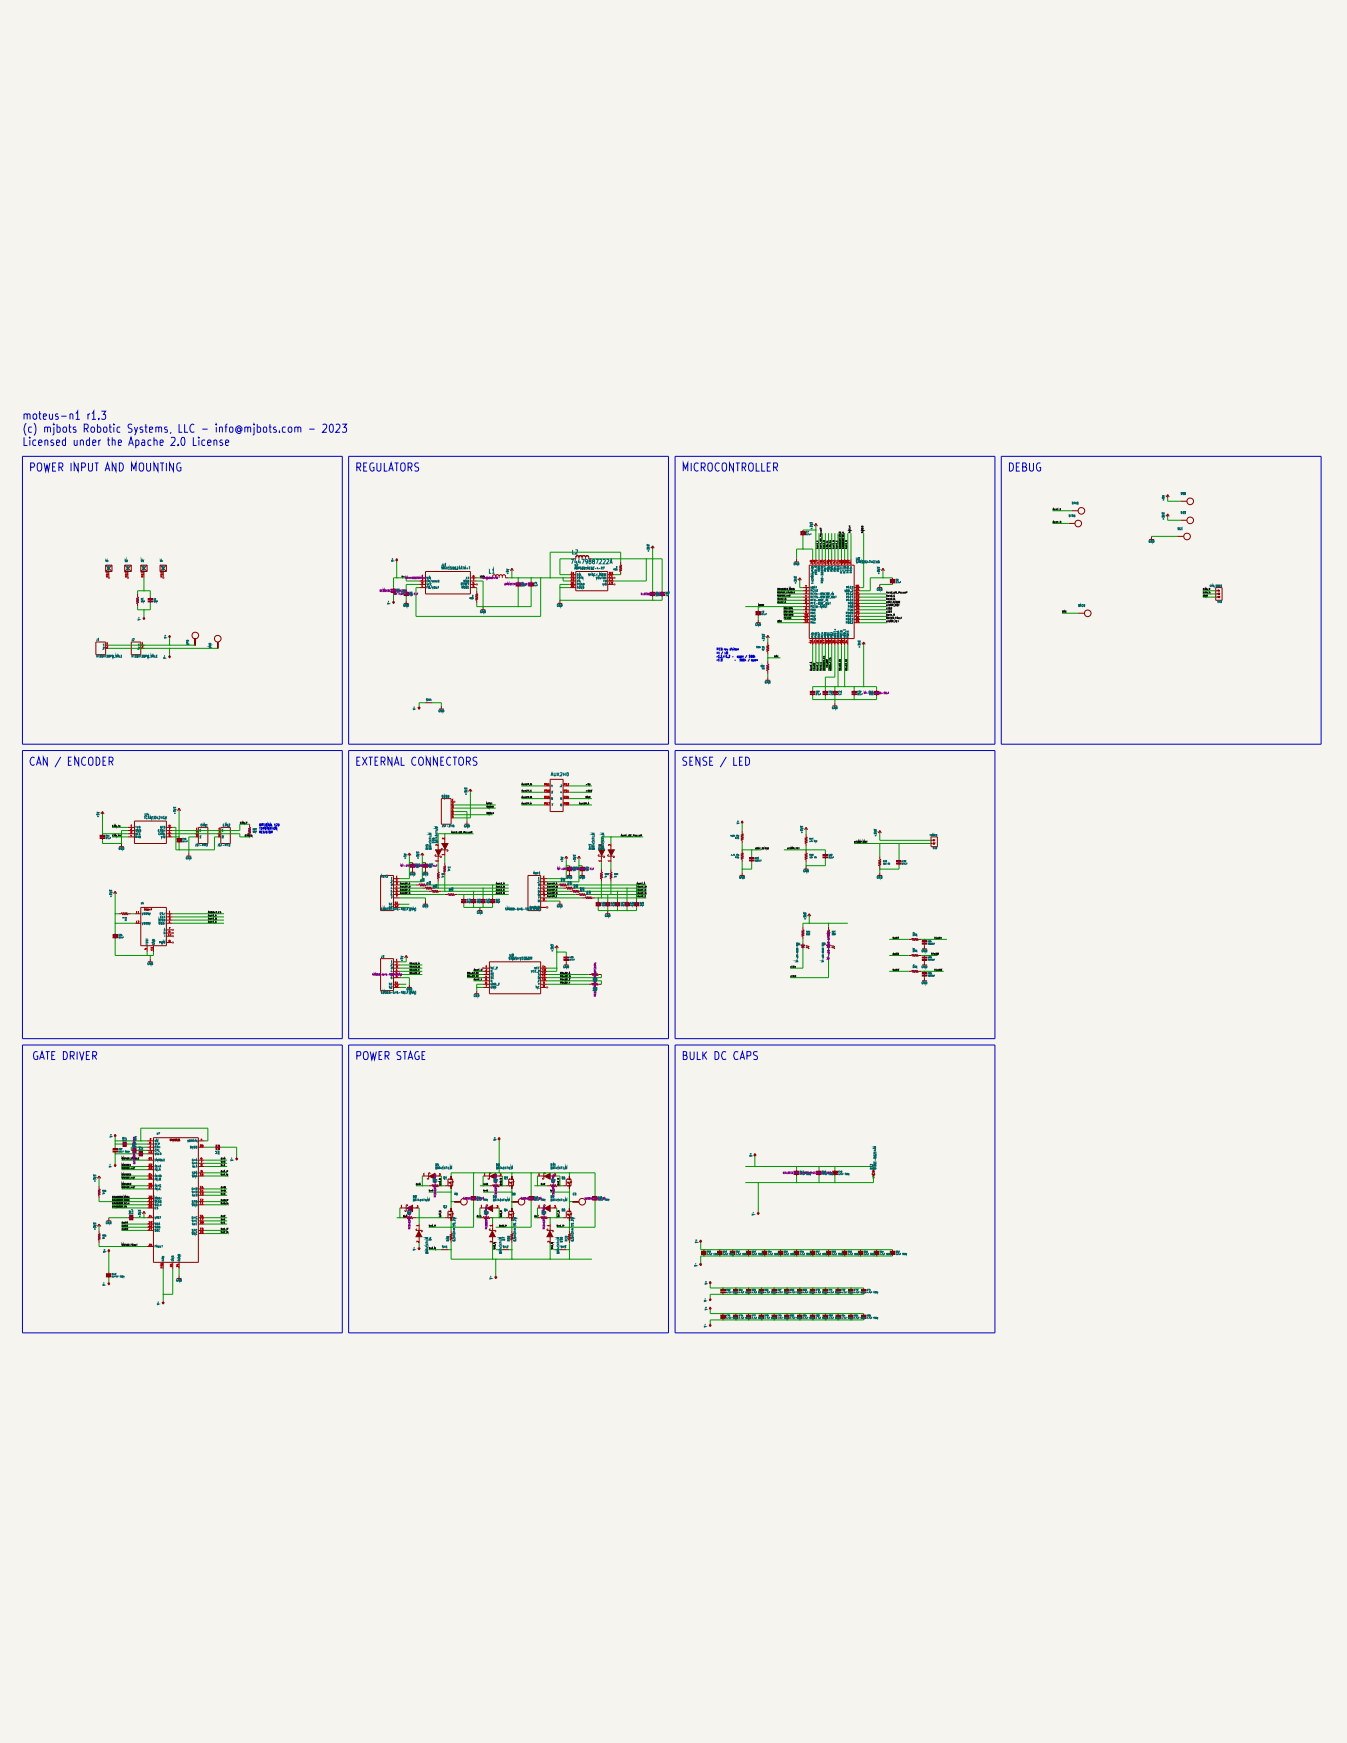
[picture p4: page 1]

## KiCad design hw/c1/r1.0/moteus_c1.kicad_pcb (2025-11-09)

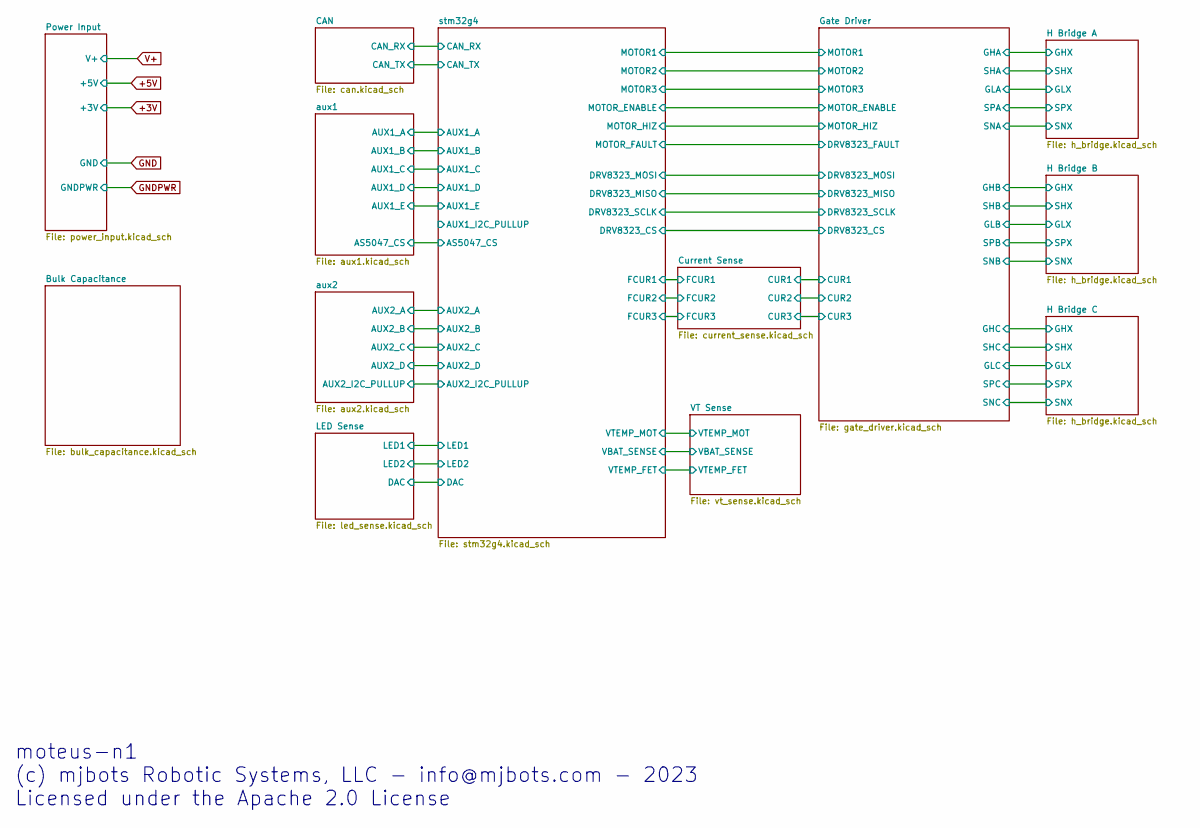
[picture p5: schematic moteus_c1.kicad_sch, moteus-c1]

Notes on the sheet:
moteus-n1 (c) mjbots Robotic Systems, LLC - info@mjbots.com - 2023 Licensed under the Apache 2.0 License

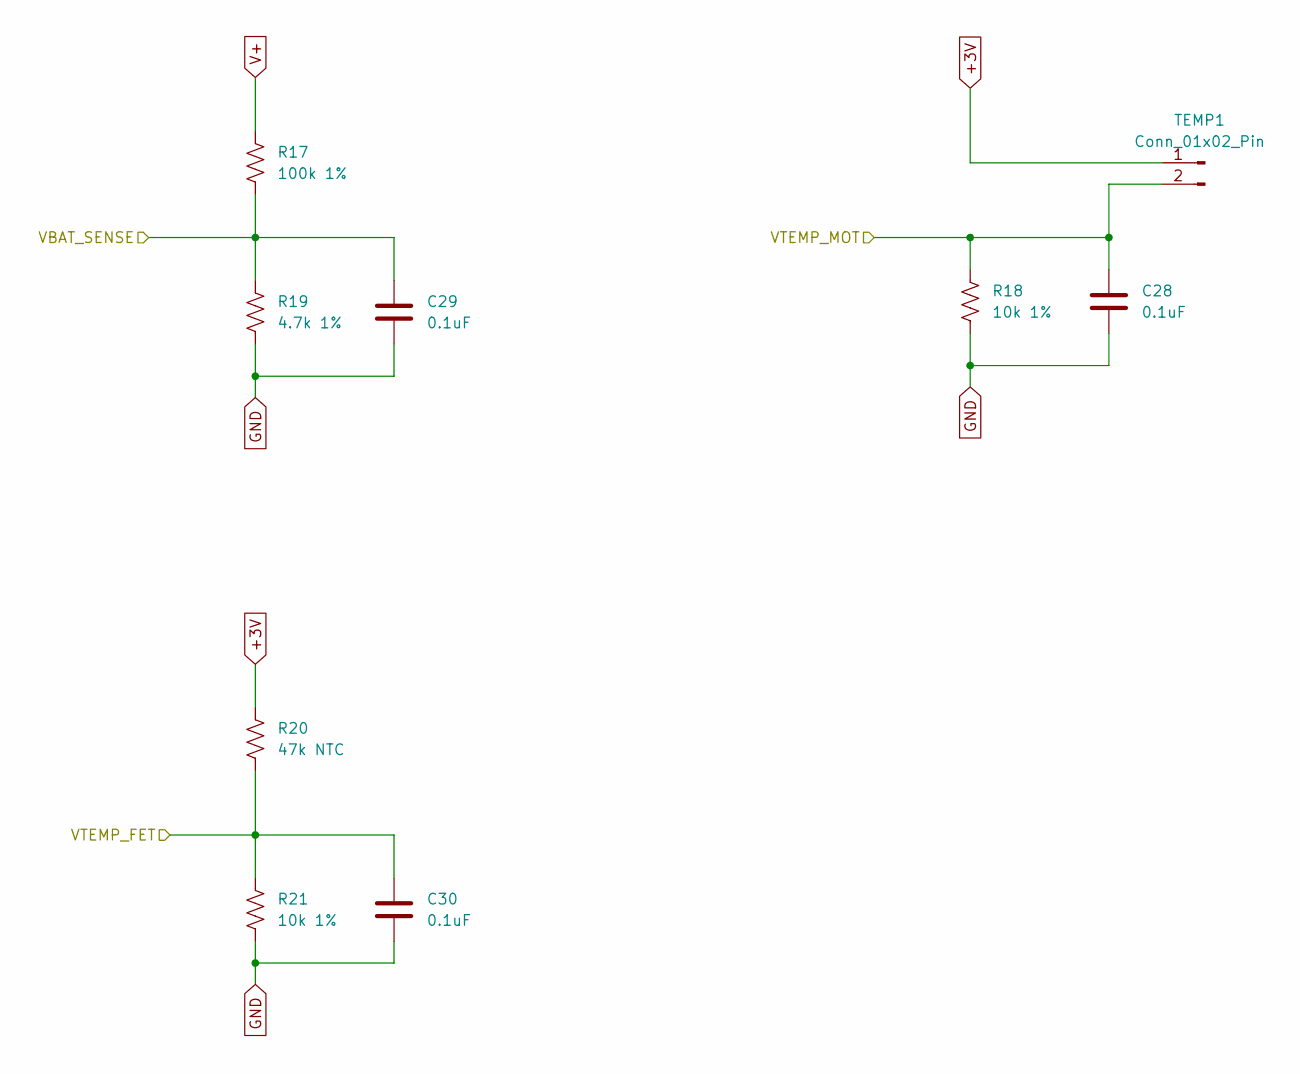
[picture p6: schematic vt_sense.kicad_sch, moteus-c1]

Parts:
C28, C29, C30: 0.1uF; C_0402_1005Metric; MPN MF-CAP-0402-0.1uF
R17: 100k 1%; R_0402_1005Metric; MPN RC0402FR-07100KL
R18, R21: 10k 1%; R_0402_1005Metric; MPN RC0402FR-0710KL
R19: 4.7k 1%; R_0402_1005Metric; MPN RC0402FR-074K7L
R20: 47k NTC; R_0402_1005Metric; MPN NCP15WB473F03RC
TEMP1: Conn_01x02_Pin; PinHeader_1x02_P2.00mm_Vertical

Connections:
/VT Sense/VBAT_SENSE: C29.1, R17.2, R19.1; also elsewhere on the board
/VT Sense/VTEMP_FET: C30.1, R20.2, R21.1; also elsewhere on the board
/VT Sense/VTEMP_MOT: C28.1, R18.1, TEMP1.2; also elsewhere on the board
V+: R17.1; also elsewhere on the board

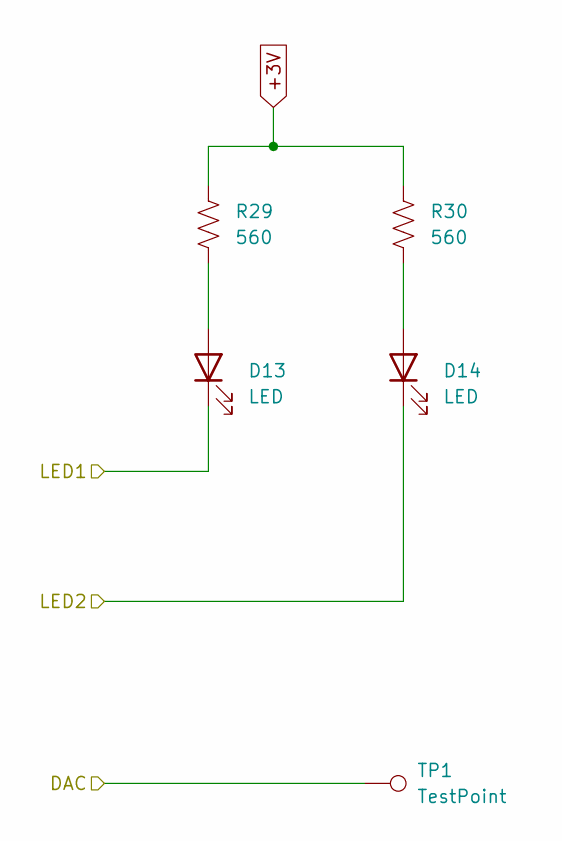
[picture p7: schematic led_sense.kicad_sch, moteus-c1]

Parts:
D13: LED; LED_0603_1608Metric; MPN MF-LED-0603-RED
D14: LED; LED_0603_1608Metric; MPN MF-LED-0603-GREEN
R29, R30: 560; R_0402_1005Metric; MPN MF-RES-0402-560
TP1: TestPoint; TestPoint_THTPad_D1.0mm_Drill0.5mm

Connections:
/LED Sense/LED1: D13.1 (K); also elsewhere on the board
/LED Sense/LED2: D14.1 (K); also elsewhere on the board
unnamed: D13.2 (A), R29.2
unnamed: D14.2 (A), R30.2

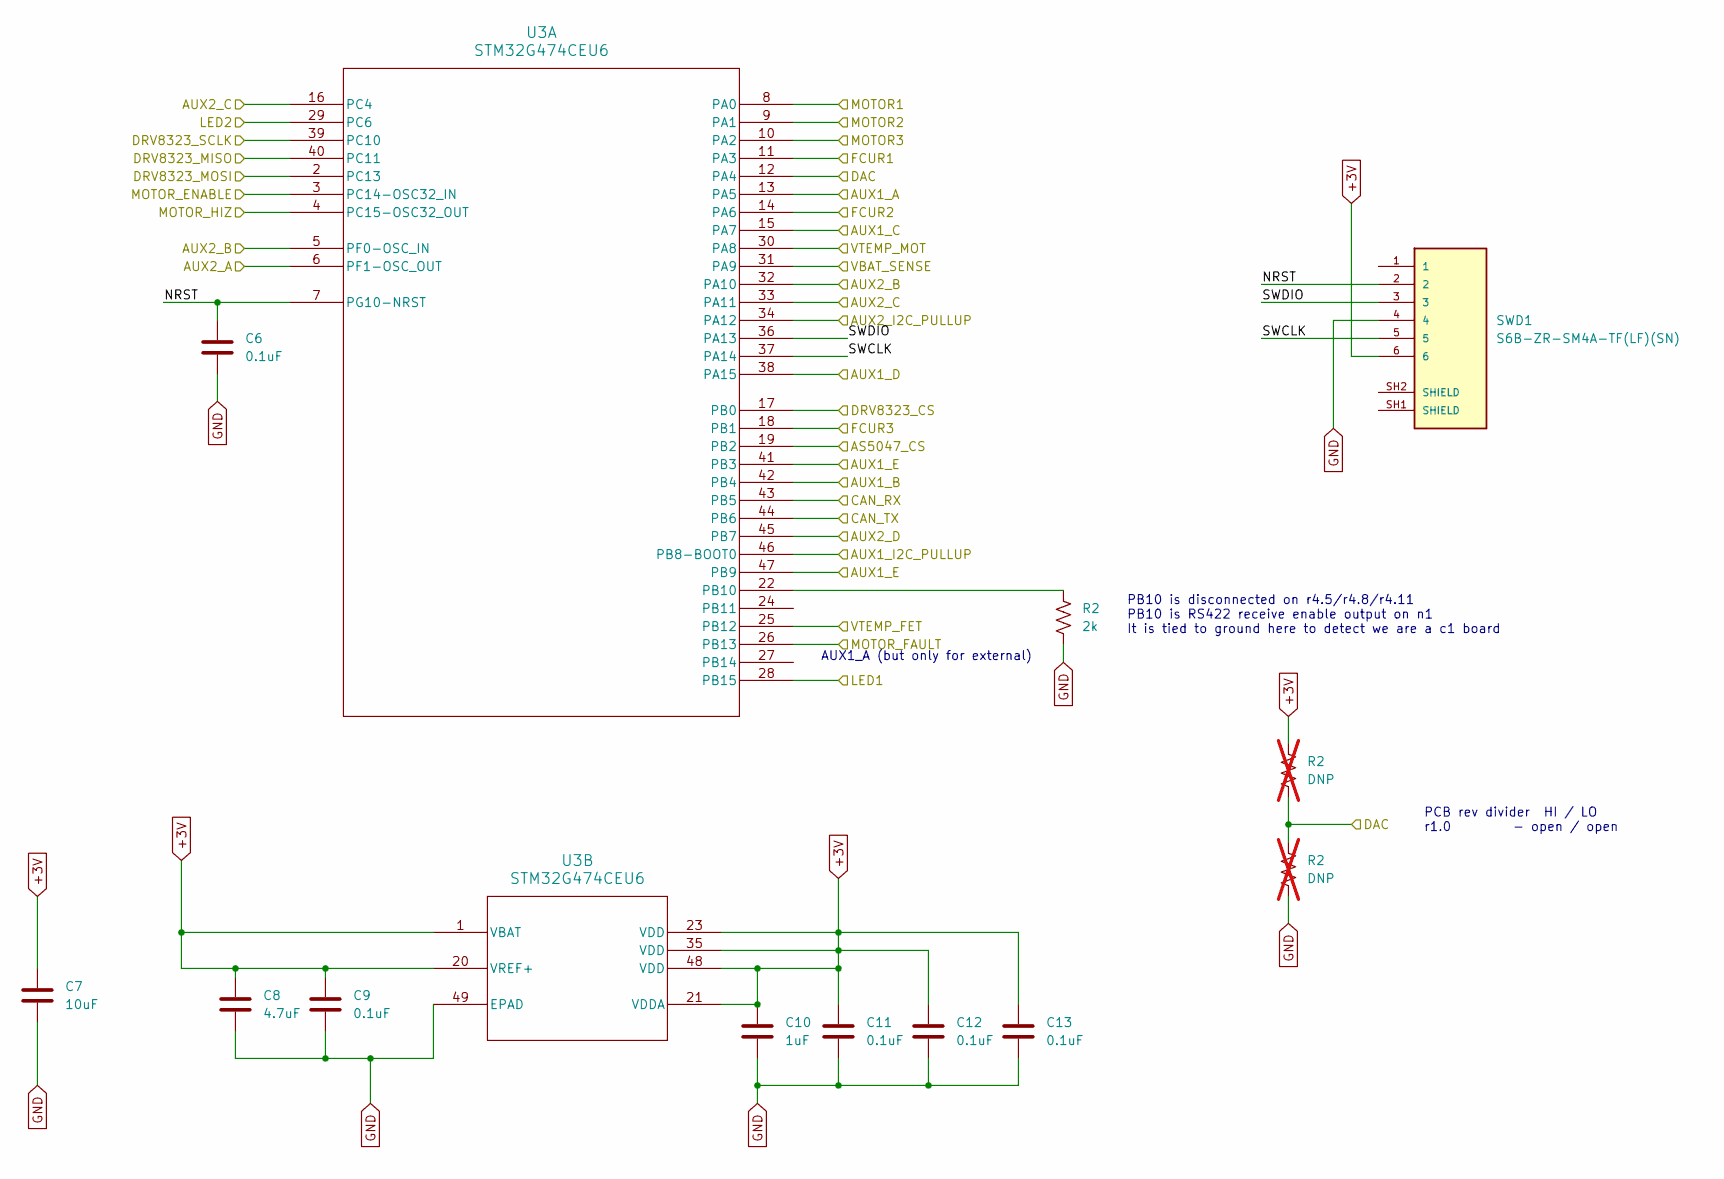
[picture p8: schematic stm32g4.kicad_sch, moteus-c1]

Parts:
C6, C9, C11, C12, C13: 0.1uF; C_0402_1005Metric; MPN MF-CAP-0402-0.1uF
C7: 10uF; C_1206_3216Metric; MPN MF-CAP-1206-10uF
C8: 4.7uF; C_0603_1608Metric; MPN CL10A475KP8NNNC
C10: 1uF; C_0402_1005Metric; MPN MF-CAP-0402-1uF
R2: 2k; R_0402_1005Metric; MPN MF-RES-0402-2K
SWD1: S6B-ZR-SM4A-TF(LF)(SN); JST_S6B-ZR-SM4A-TF(LF)(SN); MPN S6B-ZR-SM4A-TF(LF)(SN)
U3: STM32G474CEU6; UFQFPN-48_7X7X0P55MM; MPN STM32G474CEU6

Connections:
/CAN/CAN_RX: U3.43 (PB5); also elsewhere on the board
/CAN/CAN_TX: U3.44 (PB6); also elsewhere on the board
/Current Sense/FCUR1: U3.11 (PA3); also elsewhere on the board
/Current Sense/FCUR2: U3.14 (PA6); also elsewhere on the board
/Current Sense/FCUR3: U3.18 (PB1); also elsewhere on the board
/Gate Driver/DRV8323_CS: U3.17 (PB0); also elsewhere on the board
/Gate Driver/DRV8323_FAULT: U3.26 (PB13); also elsewhere on the board
/Gate Driver/DRV8323_MOSI: U3.2 (PC13); also elsewhere on the board
/Gate Driver/DRV8323_SCLK: U3.39 (PC10); also elsewhere on the board
/Gate Driver/MOTOR1: U3.8 (PA0); also elsewhere on the board
/Gate Driver/MOTOR2: U3.9 (PA1); also elsewhere on the board
/Gate Driver/MOTOR3: U3.10 (PA2); also elsewhere on the board
/Gate Driver/MOTOR_ENABLE: U3.3 (PC14-OSC32_IN); also elsewhere on the board
/Gate Driver/MOTOR_HIZ: U3.4 (PC15-OSC32_OUT); also elsewhere on the board
/LED Sense/LED1: U3.28 (PB15); also elsewhere on the board
/LED Sense/LED2: U3.29 (PC6); also elsewhere on the board
/VT Sense/VBAT_SENSE: U3.31 (PA9); also elsewhere on the board
/VT Sense/VTEMP_FET: U3.25 (PB12); also elsewhere on the board
/VT Sense/VTEMP_MOT: U3.30 (PA8); also elsewhere on the board
/aux1/AS5047_CS: U3.19 (PB2); also elsewhere on the board
/aux1/AUX1_A: U3.13 (PA5); also elsewhere on the board
/aux1/AUX1_B: U3.42 (PB4); also elsewhere on the board
/aux1/AUX1_C: U3.15 (PA7); also elsewhere on the board
/aux1/AUX1_D: U3.38 (PA15); also elsewhere on the board
/aux1/AUX1_E: U3.41 (PB3), U3.47 (PB9); also elsewhere on the board
/aux2/AUX2_A: U3.6 (PF1-OSC_OUT); also elsewhere on the board
/aux2/AUX2_B: U3.5 (PF0-OSC_IN), U3.32 (PA10); also elsewhere on the board
/aux2/AUX2_C: U3.16 (PC4), U3.33 (PA11); also elsewhere on the board
/aux2/AUX2_D: U3.45 (PB7); also elsewhere on the board
/aux2/AUX2_I2C_PULLUP: U3.34 (PA12); also elsewhere on the board
/stm32g4/AUX1_I2C_PULLUP: U3.46 (PB8-BOOT0)
/stm32g4/NRST: C6.1, SWD1.2, U3.7 (PG10-NRST)
/stm32g4/SWCLK: SWD1.5, U3.37 (PA14)
/stm32g4/SWDIO: SWD1.3, U3.36 (PA13)

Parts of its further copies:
R31: 2k; R_0402_1005Metric; MPN MF-RES-0402-2K

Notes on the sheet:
PB10 is disconnected on r4.5/r4.8/r4.11 PB10 is RS422 receive enable output on n1 It is tied to ground here to detect we are a c1 board
PCB rev divider HI / LO r1.0 - open / open
AUX1_A (but only for external)

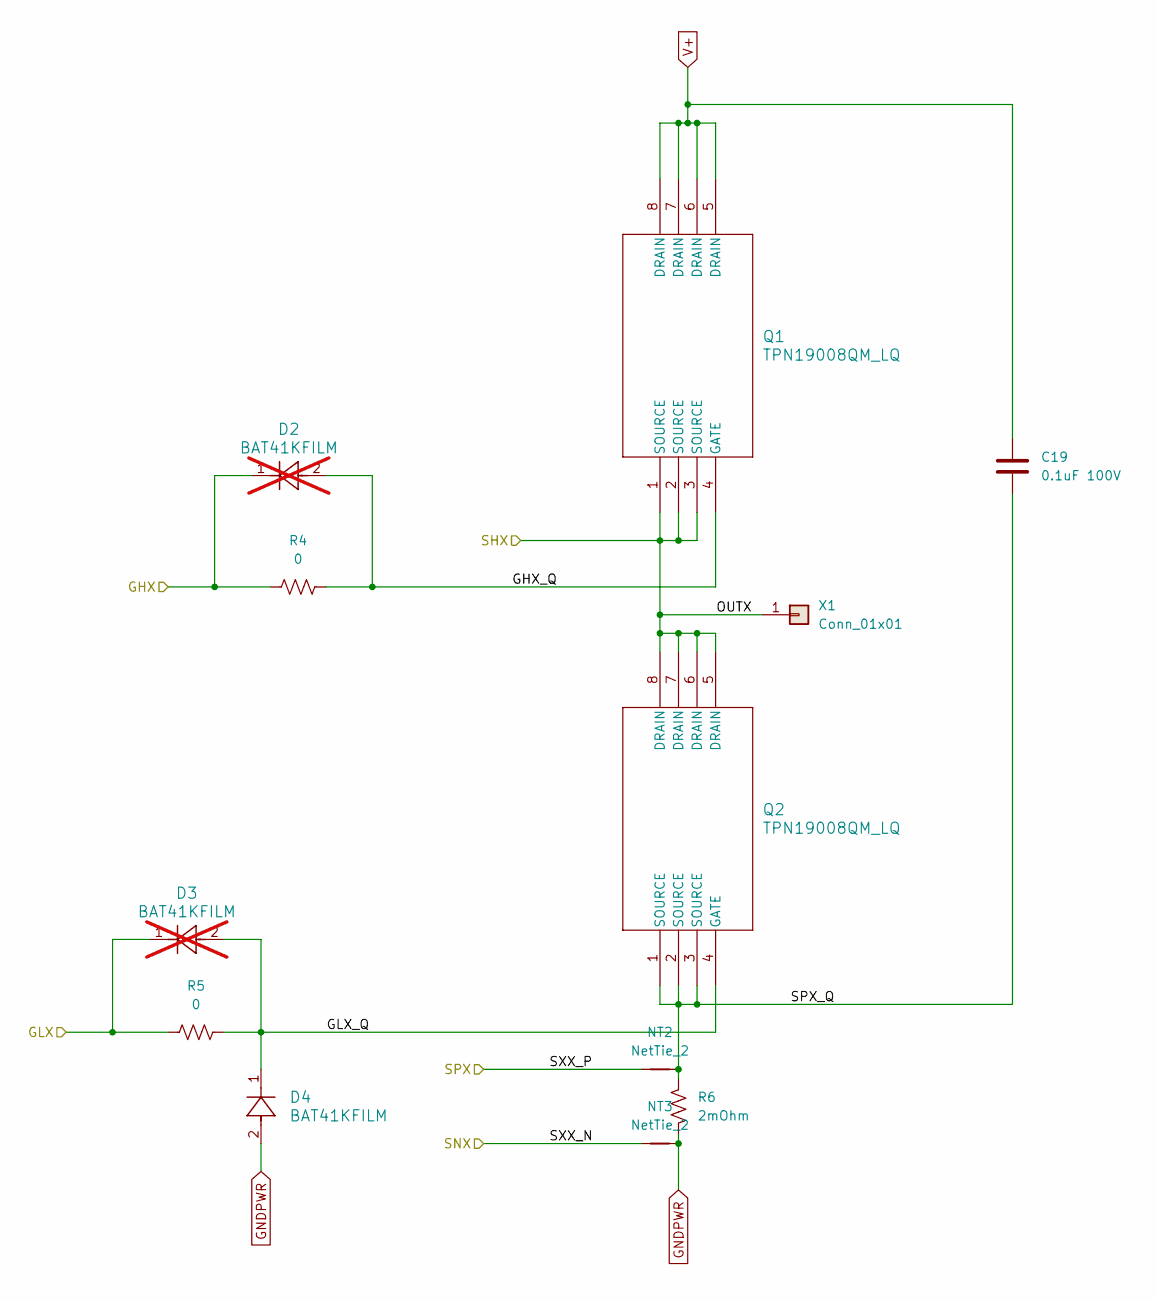
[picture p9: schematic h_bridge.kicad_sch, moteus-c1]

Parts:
C19: 0.1uF 100V; C_1206_3216Metric; MPN 12061C104KAT2A
D2, D3: BAT41KFILM; SOD-523_STM; MPN BAT41KFILM; not fitted
D4: BAT41KFILM; SOD-523_STM; MPN BAT41KFILM
NT2, NT3: NetTie_2; NetTie-2_SMD_Pad0.254mm
Q1, Q2: TPN19008QM_LQ; TSON Advance_TOS; MPN TPN19008QM,LQ
R4: 0; R_0402_1005Metric; MPN MF-RES-0402-0
R5: 0; R_0805_2012Metric; MPN MF-RES-0402-0
R6: 2mOhm; R_0805_2012Metric; MPN CSSH0805FT2L00
X1: Conn_01x01; POWER_M2.5

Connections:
/Gate Driver/GHA: D2.1, R4.1; also elsewhere on the board
/Gate Driver/GLA: D3.1, R5.1; also elsewhere on the board
/H Bridge A/GHX_Q: D2.2, Q1.4 (GATE), R4.2
/H Bridge A/GLX_Q: D3.2, D4.1, Q2.4 (GATE), R5.2
/H Bridge A/OUTX: Q1.1 (SOURCE), Q1.2 (SOURCE), Q1.3 (SOURCE), Q2.5 (DRAIN), Q2.6 (DRAIN), Q2.7 (DRAIN), Q2.8 (DRAIN), X1.1; also elsewhere on the board
/H Bridge A/SPX_Q: C19.2, NT2.2, Q2.1 (SOURCE), Q2.2 (SOURCE), Q2.3 (SOURCE), R6.1
/H Bridge A/SXX_N: NT3.1; also elsewhere on the board
/H Bridge A/SXX_P: NT2.1; also elsewhere on the board
GNDPWR: D4.2, NT3.2, R6.2; also elsewhere on the board
V+: C19.1, Q1.5 (DRAIN), Q1.6 (DRAIN), Q1.7 (DRAIN), Q1.8 (DRAIN); also elsewhere on the board

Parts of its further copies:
C20, C21: 0.1uF 100V; C_1206_3216Metric; MPN 12061C104KAT2A
D5, D6, D8, D9: BAT41KFILM; SOD-523_STM; MPN BAT41KFILM; not fitted
D7, D10: BAT41KFILM; SOD-523_STM; MPN BAT41KFILM
NT4, NT5, NT6, NT7: NetTie_2; NetTie-2_SMD_Pad0.254mm
Q3, Q4, Q5, Q6: TPN19008QM_LQ; TSON Advance_TOS; MPN TPN19008QM,LQ
R7, R10: 0; R_0402_1005Metric; MPN MF-RES-0402-0
R8, R11: 0; R_0805_2012Metric; MPN MF-RES-0402-0
R9, R12: 2mOhm; R_0805_2012Metric; MPN CSSH0805FT2L00
X2, X3: Conn_01x01; POWER_M2.5

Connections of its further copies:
/Gate Driver/GHB: D5.1, R7.1; also elsewhere on the board
/Gate Driver/GHC: D8.1, R10.1; also elsewhere on the board
/Gate Driver/GLB: D6.1, R8.1; also elsewhere on the board
/Gate Driver/GLC: D9.1, R11.1; also elsewhere on the board
/H Bridge B/GHX_Q: D5.2, Q3.4 (GATE), R7.2
/H Bridge B/GLX_Q: D6.2, D7.1, Q4.4 (GATE), R8.2
/H Bridge B/OUTX: Q3.1 (SOURCE), Q3.2 (SOURCE), Q3.3 (SOURCE), Q4.5 (DRAIN), Q4.6 (DRAIN), Q4.7 (DRAIN), Q4.8 (DRAIN), X2.1; also elsewhere on the board
/H Bridge B/SPX_Q: C20.2, NT4.2, Q4.1 (SOURCE), Q4.2 (SOURCE), Q4.3 (SOURCE), R9.1
/H Bridge B/SXX_N: NT5.1; also elsewhere on the board
/H Bridge B/SXX_P: NT4.1; also elsewhere on the board
/H Bridge C/GHX_Q: D8.2, Q5.4 (GATE), R10.2
/H Bridge C/GLX_Q: D9.2, D10.1, Q6.4 (GATE), R11.2
/H Bridge C/OUTX: Q5.1 (SOURCE), Q5.2 (SOURCE), Q5.3 (SOURCE), Q6.5 (DRAIN), Q6.6 (DRAIN), Q6.7 (DRAIN), Q6.8 (DRAIN), X3.1; also elsewhere on the board
/H Bridge C/SPX_Q: C21.2, NT6.2, Q6.1 (SOURCE), Q6.2 (SOURCE), Q6.3 (SOURCE), R12.1
/H Bridge C/SXX_N: NT7.1; also elsewhere on the board
/H Bridge C/SXX_P: NT6.1; also elsewhere on the board
GNDPWR: D7.2, D10.2, NT5.2, NT7.2, R9.2, R12.2; also elsewhere on the board
V+: C20.1, C21.1, Q3.5 (DRAIN), Q3.6 (DRAIN), Q3.7 (DRAIN), Q3.8 (DRAIN), Q5.5 (DRAIN), Q5.6 (DRAIN), Q5.7 (DRAIN), Q5.8 (DRAIN); also elsewhere on the board

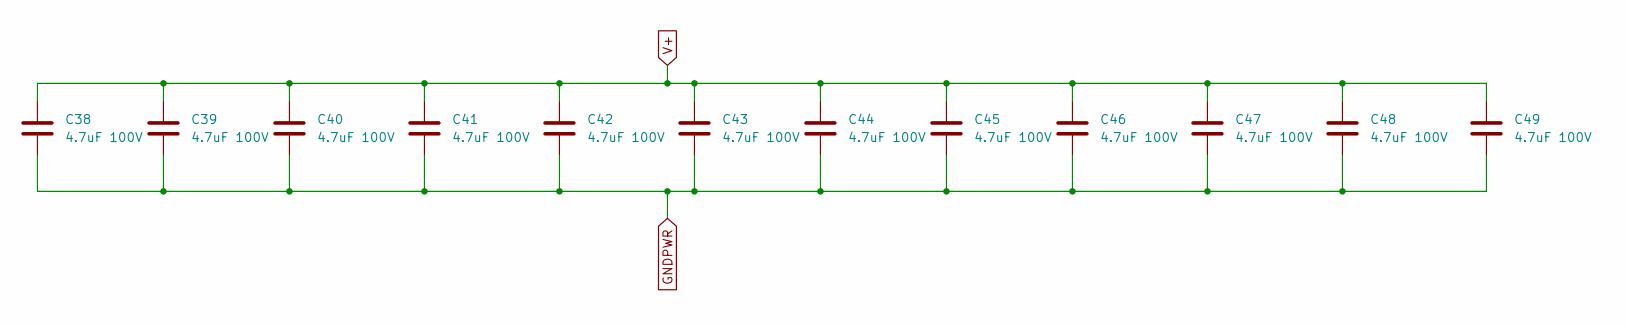
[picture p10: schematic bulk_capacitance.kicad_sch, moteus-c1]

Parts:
C38, C39, C40, C41, C42, C43, C44, C45, C46, C47, C48, C49: 4.7uF 100V; C_1206_3216Metric; MPN GRJ31CC72A475KE01K

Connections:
GNDPWR: C38.2, C39.2, C40.2, C41.2, C42.2, C43.2, C44.2, C45.2, C46.2, C47.2, C48.2, C49.2; also elsewhere on the board
V+: C38.1, C39.1, C40.1, C41.1, C42.1, C43.1, C44.1, C45.1, C46.1, C47.1, C48.1, C49.1; also elsewhere on the board

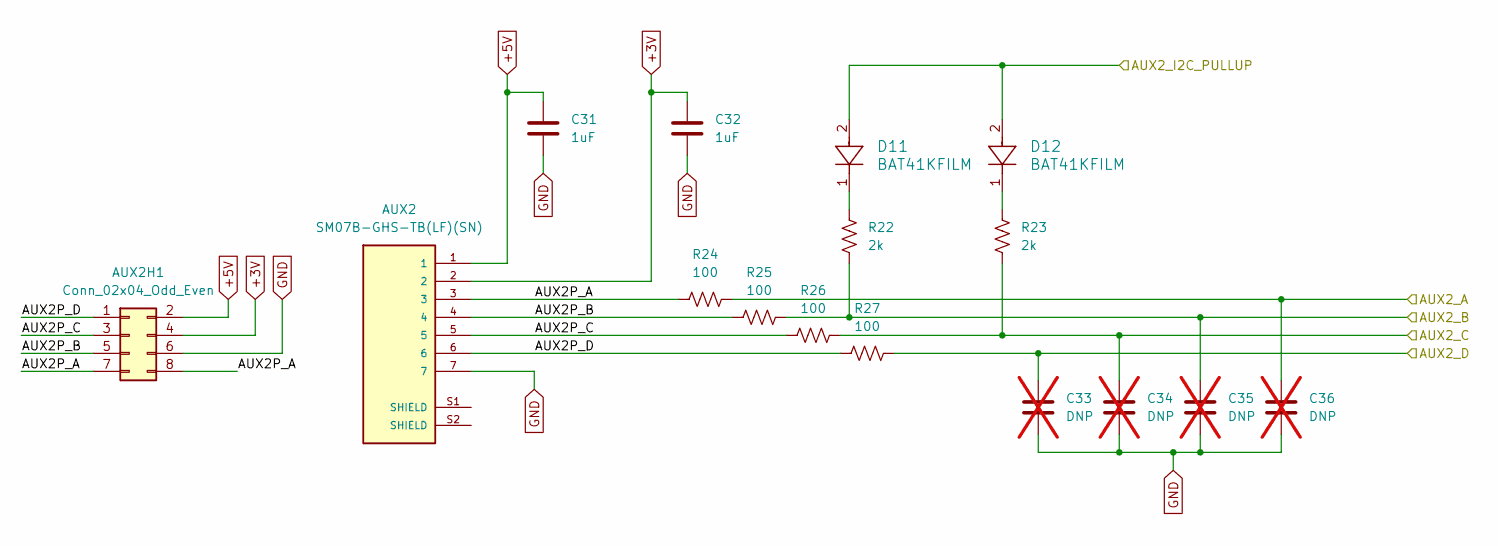
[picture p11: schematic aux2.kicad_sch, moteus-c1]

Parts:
AUX2: SM07B-GHS-TB(LF)(SN); JST_SM07B-GHS-TB(LF)(SN); MPN SM07B-GHS-TB(LF)(SN)
AUX2H1: Conn_02x04_Odd_Even; PinHeader_2x04_P1.27mm_Vertical
C31, C32: 1uF; C_0402_1005Metric; MPN MF-CAP-0402-1uF
C33, C34, C35, C36: DNP; C_0402_1005Metric; not fitted
D11, D12: BAT41KFILM; SOD-523_STM; MPN BAT41KFILM
R22, R23: 2k; R_0402_1005Metric; MPN MF-RES-0402-2K
R24, R25, R26, R27: 100; R_0402_1005Metric; MPN MF-RES-0402-100

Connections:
+5V: AUX2.1, AUX2H1.2, C31.1; also elsewhere on the board
/aux2/AUX2P_B: AUX2.4, AUX2H1.5, R25.1
/aux2/AUX2P_C: AUX2.5, AUX2H1.3, R26.1
/aux2/AUX2P_D: AUX2.6, AUX2H1.1, R27.1
/aux2/AUX2_A: C36.1, R24.2; also elsewhere on the board
/aux2/AUX2_B: C35.1, R22.2, R25.2; also elsewhere on the board
/aux2/AUX2_C: C34.1, R23.2, R26.2; also elsewhere on the board
/aux2/AUX2_D: C33.1, R27.2; also elsewhere on the board
/aux2/AUX2_I2C_PULLUP: D11.2, D12.2; also elsewhere on the board
unnamed: D11.1, R22.1
unnamed: D12.1, R23.1

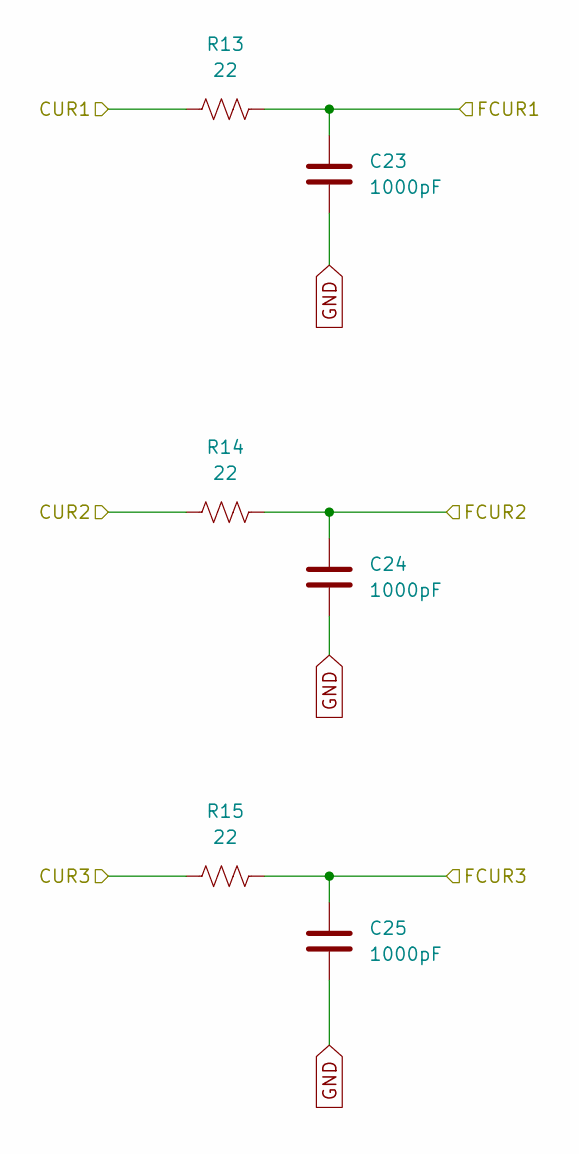
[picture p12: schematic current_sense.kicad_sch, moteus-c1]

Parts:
C23, C24, C25: 1000pF; C_0402_1005Metric; MPN MF-CAP-0402-1nF
R13, R14, R15: 22; R_0402_1005Metric; MPN MF-RES-0402-22

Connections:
/Current Sense/CUR1: R13.1; also elsewhere on the board
/Current Sense/CUR2: R14.1; also elsewhere on the board
/Current Sense/CUR3: R15.1; also elsewhere on the board
/Current Sense/FCUR1: C23.1, R13.2; also elsewhere on the board
/Current Sense/FCUR2: C24.1, R14.2; also elsewhere on the board
/Current Sense/FCUR3: C25.1, R15.2; also elsewhere on the board

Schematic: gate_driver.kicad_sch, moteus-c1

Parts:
C14: 1uF 25V; C_0603_1608Metric; MPN C1608X7R1E105K080AE
C15: 0.1uF 100V; C_0603_1608Metric; MPN GCJ188R72A104KA01D
C16: 47nF 100V; C_0603_1608Metric; MPN C0603X473K1RAC7867
C17: 1uF; C_0402_1005Metric; MPN MF-CAP-0402-1uF
C18: 1uF; C_0603_1608Metric; MPN MF-CAP-0603-1uF
R2, R3: 2k; R_0402_1005Metric; MPN MF-RES-0402-2K
U4: DRV8323SRTAR; RTA0040B; MPN DRV8323SRTAR

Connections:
/Current Sense/CUR1: U4.21 (SOC); also elsewhere on the board
/Current Sense/CUR2: U4.22 (SOB); also elsewhere on the board
/Current Sense/CUR3: U4.23 (SOA); also elsewhere on the board
/Gate Driver/DRV8323_CS: U4.29 (GAIN_SCS_N); also elsewhere on the board
/Gate Driver/DRV8323_FAULT: R3.2, U4.25 (FAULT_N); also elsewhere on the board
/Gate Driver/DRV8323_MOSI: U4.27 (IDRIVE_SDI); also elsewhere on the board
/Gate Driver/DRV8323_SCLK: U4.28 (VDS_SCLK); also elsewhere on the board
/Gate Driver/GHA: U4.6 (GHA); also elsewhere on the board
/Gate Driver/GHB: U4.15 (GHB); also elsewhere on the board
/Gate Driver/GHC: U4.16 (GHC); also elsewhere on the board
/Gate Driver/GLA: U4.8 (GLA); also elsewhere on the board
/Gate Driver/GLB: U4.13 (GLB); also elsewhere on the board
/Gate Driver/GLC: U4.18 (GLC); also elsewhere on the board
/Gate Driver/MOTOR1: U4.34 (INHA); also elsewhere on the board
/Gate Driver/MOTOR2: U4.36 (INHB); also elsewhere on the board
/Gate Driver/MOTOR3: U4.38 (INHC); also elsewhere on the board
/Gate Driver/MOTOR_ENABLE: U4.30 (ENABLE); also elsewhere on the board
/Gate Driver/MOTOR_HIZ: U4.35 (INLA), U4.37 (INLB), U4.39 (INLC); also elsewhere on the board
/H Bridge A/OUTX: U4.7 (SHA); also elsewhere on the board
/H Bridge A/SXX_N: U4.10 (SNA); also elsewhere on the board
/H Bridge A/SXX_P: U4.9 (SPA); also elsewhere on the board
/H Bridge B/OUTX: U4.14 (SHB); also elsewhere on the board
/H Bridge B/SXX_N: U4.11 (SNB); also elsewhere on the board
/H Bridge B/SXX_P: U4.12 (SPB); also elsewhere on the board
/H Bridge C/OUTX: U4.17 (SHC); also elsewhere on the board
/H Bridge C/SXX_N: U4.20 (SNC); also elsewhere on the board
/H Bridge C/SXX_P: U4.19 (SPC); also elsewhere on the board
GNDPWR: C15.1, U4.40 (PGND), U4.41 (PAD); also elsewhere on the board
unnamed: C16.2, U4.2 (CPH)
unnamed: C16.1, U4.1 (CPL)
unnamed: C17.2, U4.33 (DVDD)
unnamed: C14.2, U4.3 (VCP)
V+: C14.1, C15.2, U4.4 (VM), U4.5 (VDRAIN); also elsewhere on the board

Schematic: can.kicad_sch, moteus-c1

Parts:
C26, C27: 0.1uF; C_0402_1005Metric; MPN MF-CAP-0402-0.1uF
CAN1: S3B-PH-SM4-TB(LF)(SN); JST_S3B-PH-SM4-TB(LF)(SN); MPN S3B-PH-SM4-TB(LF)(SN)
CAN_DBG1: Conn_01x03_Pin; PinHeader_1x03_P2.00mm_Vertical
R16: 120; R_0805_2012Metric; MPN RC0805FR-07120RL; not fitted
U5: TCAN1057AEV-Q1; SOIC-8_3.9x4.9mm_P1.27mm; MPN TCAN1057AEVDRQ1

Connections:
+5V: C27.1, U5.3 (VCC); also elsewhere on the board
/CAN/CAN_N: CAN1.2, CAN_DBG1.2, R16.2, U5.6 (CANL)
/CAN/CAN_P: CAN1.1, CAN_DBG1.1, R16.1, U5.7 (CANH)
/CAN/CAN_RX: U5.4 (RXD); also elsewhere on the board
/CAN/CAN_TX: U5.1 (TXD); also elsewhere on the board

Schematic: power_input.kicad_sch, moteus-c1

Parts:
C1: 1uF 100V; C_0805_2012Metric; MPN GCM21BC72A105KE36L
C2: 22uF; C_1206_3216Metric; MPN GRM31CR71A226KE15L
C3, C4: 1uF; C_0402_1005Metric; MPN MF-CAP-0402-1uF
C5: 1uF; C_0603_1608Metric; MPN MF-CAP-0603-1uF
D1: SMBJ51D-M3/I; D_SMB; MPN SMBJ51D-M3/I
J1: XT30PW-M; AMASS_XT30PW-M; MPN XT30PW-M
L1: 47uH; IND_4018-WE-LQS_WRE; MPN 74404042470
NT1: NetTie_2; NetTie-2_SMD_Pad0.254mm
R1: 0; R_0402_1005Metric; MPN MF-RES-0402-0
U1: MAX15062BATA+T; 21-0487A_MXM; MPN MAX15062BATA+T
U2: TLV70233DSER; DSE0006A; MPN TLV70233DSER
VN1: Conn_01x01; POWER_M2.5
VP1: Conn_01x01; POWER_M2.5

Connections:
+5V: C2.1, C3.1, L1.1, U1.4 (FB/VOUT), U2.1 (IN); also elsewhere on the board
GNDPWR: C1.2, C5.2, D1.2 (A2), J1.N, NT1.1, VN1.1; also elsewhere on the board
unnamed: L1.2, U1.8 (LX)
unnamed: R1.1, U1.5 (MODE)
unnamed: C5.1, U1.3 (VCC)
V+: C1.1, D1.1 (A1), J1.P, U1.1 (VIN), U1.2 (EN/UVLO), VP1.1; also elsewhere on the board

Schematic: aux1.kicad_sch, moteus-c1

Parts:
AUX1: Conn_01x04; PinHeader_1x04_P1.27mm_Vertical
C37: 0.1uF; C_0402_1005Metric; MPN MF-CAP-0402-0.1uF
R24: 100; R_0402_1005Metric; MPN MF-RES-0402-100
R28: 0; R_0402_1005Metric; MPN MF-RES-0402-0
U6: AS5047P-ATSM; TSSOP14_OSM; MPN AS5047P-ATSM

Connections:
/aux1/AS5047_CS: U6.1 (CSn); also elsewhere on the board
/aux1/AUX1_A: U6.2 (CLK); also elsewhere on the board
/aux1/AUX1_B: U6.3 (MISO); also elsewhere on the board
/aux1/AUX1_C: U6.4 (MOSI); also elsewhere on the board
/aux2/AUX2_A: R24.2; also elsewhere on the board
unnamed: R28.1, U6.11 (VDD)

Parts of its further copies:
R34, R35: 100; R_0402_1005Metric; MPN MF-RES-0402-100

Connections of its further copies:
/aux1/AUX1_D: R34.2; also elsewhere on the board
/aux1/AUX1_E: R35.2; also elsewhere on the board

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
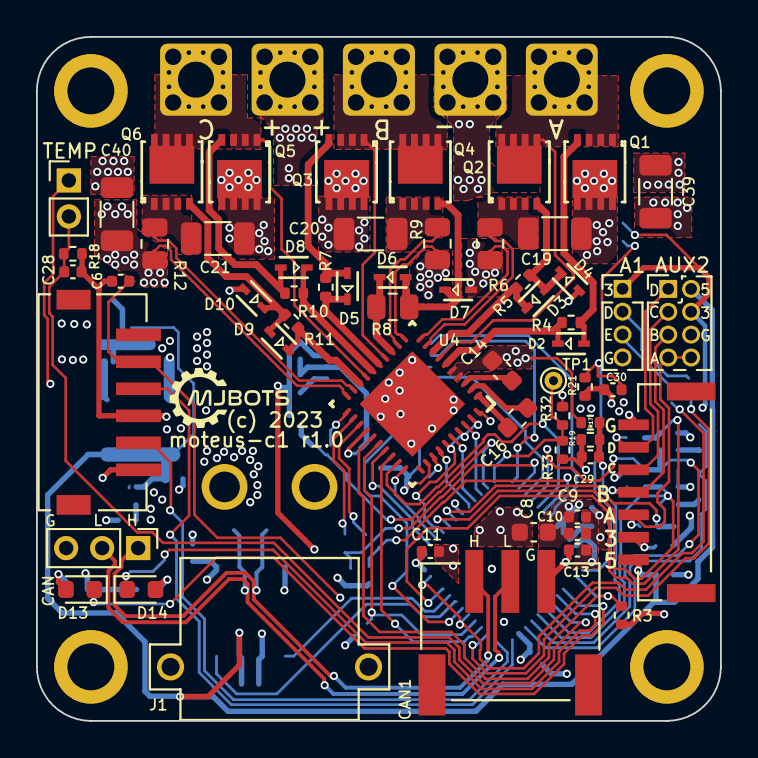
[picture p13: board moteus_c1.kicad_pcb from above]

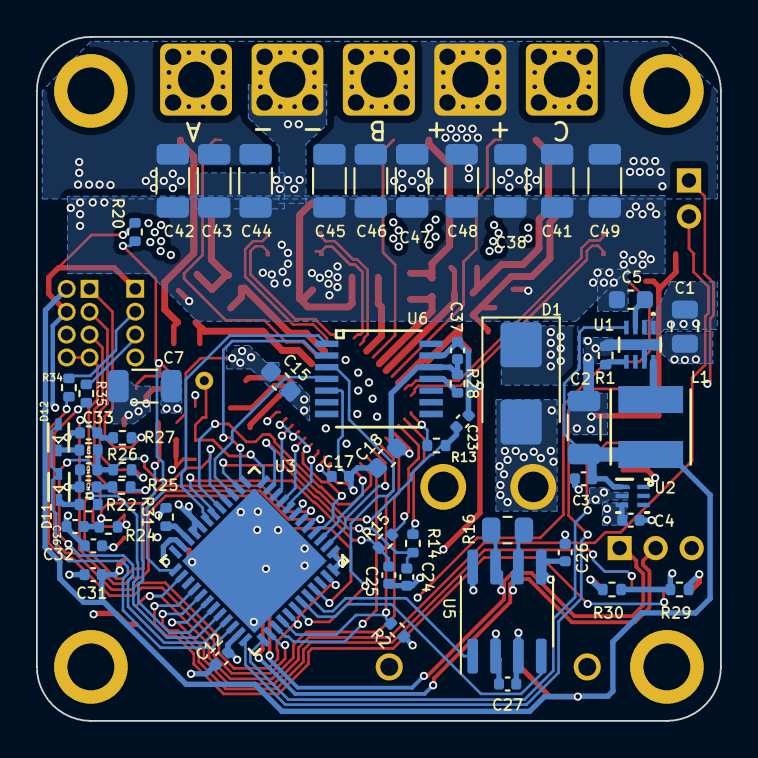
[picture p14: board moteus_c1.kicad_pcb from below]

Board: 4 copper layers, 38.0 x 38.0 mm, 135 parts (61 on the bottom side), 88 nets.

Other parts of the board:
MOUNT1, MOUNT2, MOUNT3, MOUNT4: M2.5_MOUNT
R32, R33: DNP; R_0402_1005Metric

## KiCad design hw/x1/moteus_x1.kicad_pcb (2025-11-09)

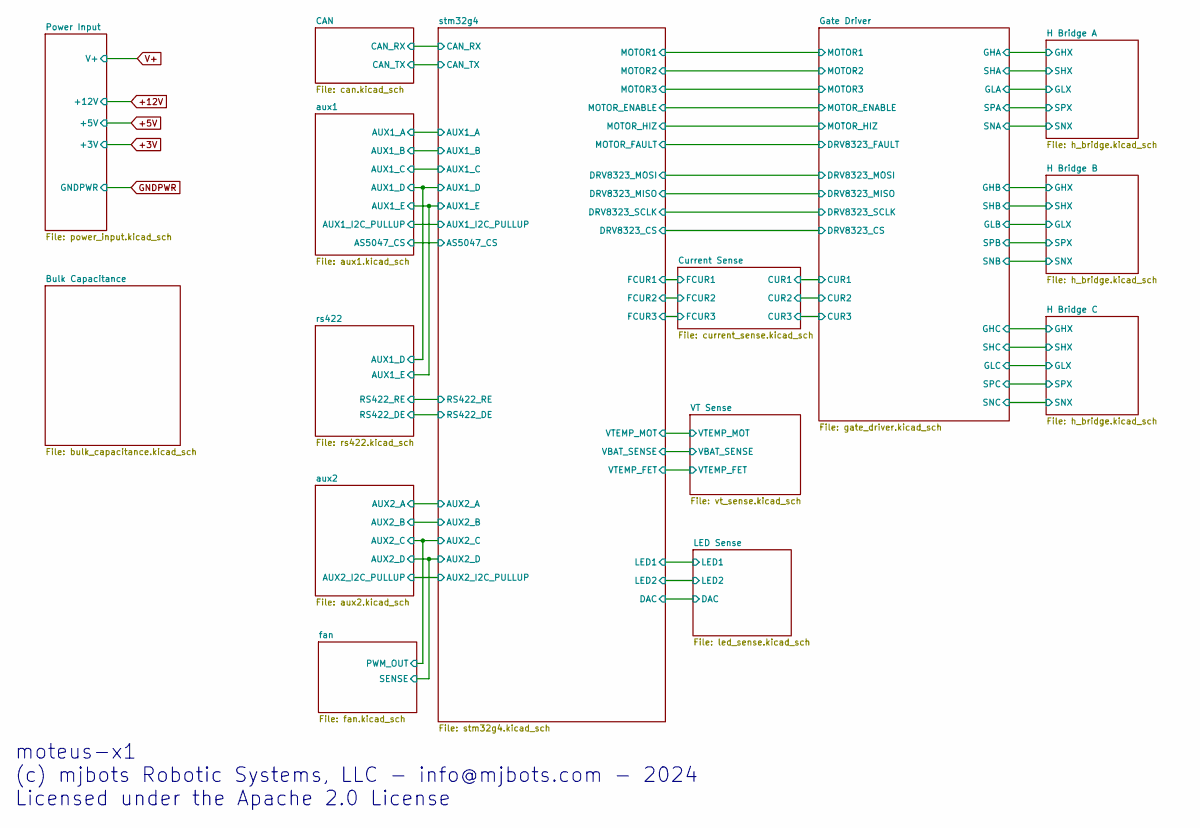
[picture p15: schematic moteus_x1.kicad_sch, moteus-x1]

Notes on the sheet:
moteus-x1 (c) mjbots Robotic Systems, LLC - info@mjbots.com - 2024 Licensed under the Apache 2.0 License

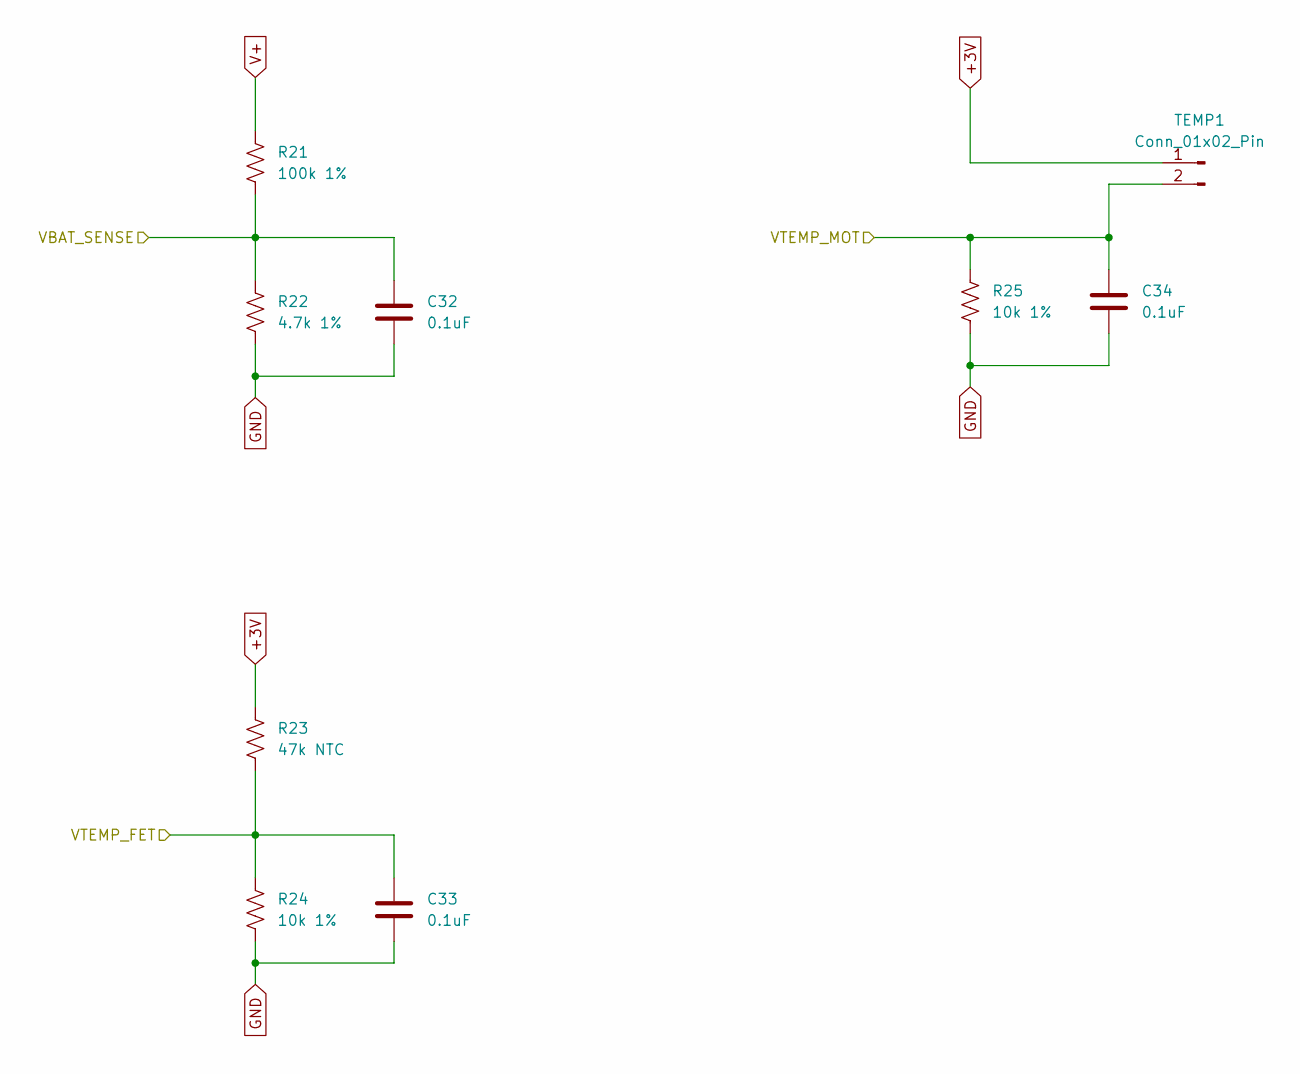
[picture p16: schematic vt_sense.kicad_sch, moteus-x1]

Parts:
C32, C33, C34: 0.1uF; C_0402_1005Metric; MPN MF-CAP-0402-0.1uF
R21: 100k 1%; R_0402_1005Metric; MPN RC0402FR-07100KL
R22: 4.7k 1%; R_0402_1005Metric; MPN RC0402FR-074K7L
R23: 47k NTC; R_0402_1005Metric; MPN NCP15WB473F03RC
R24, R25: 10k 1%; R_0402_1005Metric; MPN RC0402FR-0710KL
TEMP1: Conn_01x02_Pin; PinHeader_1x02_P2.54mm_Vertical

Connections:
+3V: R23.1, TEMP1.1; also elsewhere on the board
/VT Sense/VBAT_SENSE: C32.1, R21.2, R22.1; also elsewhere on the board
/VT Sense/VTEMP_FET: C33.1, R23.2, R24.1; also elsewhere on the board
/VT Sense/VTEMP_MOT: C34.1, R25.1, TEMP1.2; also elsewhere on the board
GND: C32.2, C33.2, C34.2, R22.2, R24.2, R25.2; also elsewhere on the board
V+: R21.1; also elsewhere on the board


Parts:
D1: LED; LED_0603_1608Metric; MPN MF-LED-0603-RED
D2: LED; LED_0603_1608Metric; MPN MF-LED-0603-GREEN
R39, R40: 560; R_0402_1005Metric; MPN MF-RES-0402-560
TP4: TestPoint; TestPoint_THTPad_D1.0mm_Drill0.5mm

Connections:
+3V: R39.1, R40.1; also elsewhere on the board
/LED Sense/DAC: TP4.1; also elsewhere on the board
/LED Sense/LED1: D1.1 (K); also elsewhere on the board
/LED Sense/LED2: D2.1 (K); also elsewhere on the board
unnamed: D1.2 (A), R39.2
unnamed: D2.2 (A), R40.2

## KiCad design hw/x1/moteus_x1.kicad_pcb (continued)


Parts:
C10: 10uF; C_1206_3216Metric; MPN MF-CAP-1206-10uF
C11, C13, C15, C16, C17: 0.1uF; C_0402_1005Metric; MPN MF-CAP-0402-0.1uF
C12: 4.7uF; C_0603_1608Metric; MPN CL10A475KP8NNNC
C14: 1uF; C_0402_1005Metric; MPN MF-CAP-0402-1uF
R9: 2k; R_0402_1005Metric; MPN MF-RES-0402-2K
R10: DNP; R_0402_1005Metric; not fitted
R11: 100k 1%; R_0402_1005Metric; MPN RC0402FR-07100KL
SWD1: S6B-ZR-SM4A-TF(LF)(SN); JST_S6B-ZR-SM4A-TF(LF)(SN); MPN S6B-ZR-SM4A-TF(LF)(SN)
U4: STM32G474CEU6; UFQFPN-48_7X7X0P55MM; MPN STM32G474CEU6

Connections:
+3V: C10.1, C12.1, C13.1, C14.1, C15.1, C16.1, C17.1, R10.1, SWD1.6, U4.1 (VBAT), U4.20 (VREF+), U4.21 (VDDA), U4.23 (VDD), U4.35 (VDD), U4.48 (VDD); also elsewhere on the board
/CAN/CAN_RX: U4.43 (PB5); also elsewhere on the board
/CAN/CAN_TX: U4.44 (PB6); also elsewhere on the board
/Current Sense/FCUR1: U4.11 (PA3); also elsewhere on the board
/Current Sense/FCUR2: U4.14 (PA6); also elsewhere on the board
/Current Sense/FCUR3: U4.18 (PB1); also elsewhere on the board
/Gate Driver/DRV8323_CS: U4.17 (PB0); also elsewhere on the board
/Gate Driver/DRV8323_FAULT: U4.26 (PB13); also elsewhere on the board
/Gate Driver/DRV8323_MISO: U4.40 (PC11); also elsewhere on the board
/Gate Driver/DRV8323_MOSI: U4.2 (PC13); also elsewhere on the board
/Gate Driver/DRV8323_SCLK: U4.39 (PC10); also elsewhere on the board
/Gate Driver/MOTOR1: U4.8 (PA0); also elsewhere on the board
/Gate Driver/MOTOR2: U4.9 (PA1); also elsewhere on the board
/Gate Driver/MOTOR3: U4.10 (PA2); also elsewhere on the board
/Gate Driver/MOTOR_ENABLE: U4.3 (PC14-OSC32_IN); also elsewhere on the board
/Gate Driver/MOTOR_HIZ: U4.4 (PC15-OSC32_OUT); also elsewhere on the board
/LED Sense/DAC: R10.2, R11.1, U4.12 (PA4); also elsewhere on the board
/LED Sense/LED1: U4.28 (PB15); also elsewhere on the board
/LED Sense/LED2: U4.29 (PC6); also elsewhere on the board
/VT Sense/VBAT_SENSE: U4.31 (PA9); also elsewhere on the board
/VT Sense/VTEMP_FET: U4.25 (PB12); also elsewhere on the board
/VT Sense/VTEMP_MOT: U4.30 (PA8); also elsewhere on the board
/aux1/AS5047_CS: U4.19 (PB2); also elsewhere on the board
/aux1/AUX1_A: U4.13 (PA5), U4.27 (PB14); also elsewhere on the board
/aux1/AUX1_B: U4.42 (PB4); also elsewhere on the board
/aux1/AUX1_C: U4.15 (PA7); also elsewhere on the board
/aux1/AUX1_D: U4.38 (PA15); also elsewhere on the board
/aux1/AUX1_E: U4.41 (PB3), U4.47 (PB9); also elsewhere on the board
/aux1/AUX1_I2C_PULLUP: U4.46 (PB8-BOOT0); also elsewhere on the board
/aux2/AUX2_A: U4.6 (PF1-OSC_OUT); also elsewhere on the board
/aux2/AUX2_B: U4.5 (PF0-OSC_IN), U4.32 (PA10); also elsewhere on the board
/aux2/AUX2_C: U4.16 (PC4), U4.33 (PA11); also elsewhere on the board
/aux2/AUX2_D: U4.45 (PB7); also elsewhere on the board
/aux2/AUX2_I2C_PULLUP: U4.34 (PA12); also elsewhere on the board
/rs422/RS422_DE: R9.1, U4.24 (PB11); also elsewhere on the board
/rs422/RS422_RE: U4.22 (PB10); also elsewhere on the board
/stm32g4/NRST: C11.1, SWD1.2, U4.7 (PG10-NRST)
/stm32g4/SWCLK: SWD1.5, U4.37 (PA14)
/stm32g4/SWDIO: SWD1.3, U4.36 (PA13)
GND: C10.2, C11.2, C12.2, C13.2, C14.2, C15.2, C16.2, C17.2, R9.2, R11.2, SWD1.4, U4.49 (EPAD); also elsewhere on the board

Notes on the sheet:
PCB rev divider HI / LO x1 r1 - open / 100k
PCB rev divider PB10 / PB11 family 1 (n1) open / open family 2 (c1) down / open family 3 (x1) open / down


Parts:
C25: 0.1uF 100V; C_1812_4532Metric; MPN 18121C104MAT2A
D5: BAT41KFILM; SOD-523_STM; MPN BAT41KFILM
NT4, NT5: NetTie_2; NetTie-2_SMD_Pad0.2
Q3, Q4: FDMT80080DC; PQFN_8x8; MPN FDMT80080DC
R15: 0.5mOhm; R_2512_6332Metric; MPN WSLF2512L5000FEA
X2: Conn_01x01; POWER_M2.5

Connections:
/Gate Driver/GHB: Q3.1 (G); also elsewhere on the board
/Gate Driver/GLB: D5.1, Q4.1 (G); also elsewhere on the board
/H Bridge B/OUTX: Q3.2 (S), Q4.3 (D), X2.1; also elsewhere on the board
/H Bridge B/SPX_Q: C25.2, NT4.2, Q4.2 (S), R15.1
/H Bridge B/SXX_N: NT5.1; also elsewhere on the board
/H Bridge B/SXX_P: NT4.1; also elsewhere on the board
GNDPWR: D5.2, NT5.2, R15.2; also elsewhere on the board
V+: C25.1, Q3.3 (D); also elsewhere on the board

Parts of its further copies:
C24, C26: 0.1uF 100V; C_1812_4532Metric; MPN 18121C104MAT2A
D4, D6: BAT41KFILM; SOD-523_STM; MPN BAT41KFILM
NT2, NT3, NT6, NT7: NetTie_2; NetTie-2_SMD_Pad0.2
Q1, Q2, Q5, Q6: FDMT80080DC; PQFN_8x8; MPN FDMT80080DC
R14, R16: 0.5mOhm; R_2512_6332Metric; MPN WSLF2512L5000FEA
X1, X3: Conn_01x01; POWER_M2.5

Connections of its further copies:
/Gate Driver/GHA: Q1.1 (G); also elsewhere on the board
/Gate Driver/GHC: Q5.1 (G); also elsewhere on the board
/Gate Driver/GLA: D4.1, Q2.1 (G); also elsewhere on the board
/Gate Driver/GLC: D6.1, Q6.1 (G); also elsewhere on the board
/H Bridge A/OUTX: Q1.2 (S), Q2.3 (D), X1.1; also elsewhere on the board
/H Bridge A/SPX_Q: C24.2, NT2.2, Q2.2 (S), R14.1
/H Bridge A/SXX_N: NT3.1; also elsewhere on the board
/H Bridge A/SXX_P: NT2.1; also elsewhere on the board
/H Bridge C/OUTX: Q5.2 (S), Q6.3 (D), X3.1; also elsewhere on the board
/H Bridge C/SPX_Q: C26.2, NT6.2, Q6.2 (S), R16.1
/H Bridge C/SXX_N: NT7.1; also elsewhere on the board
/H Bridge C/SXX_P: NT6.1; also elsewhere on the board
GNDPWR: D4.2, D6.2, NT3.2, NT7.2, R14.2, R16.2; also elsewhere on the board
V+: C24.1, C26.1, Q1.3 (D), Q5.3 (D); also elsewhere on the board


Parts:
C45, C46, C47, C48, C49, C50, C51, C52, C53, C54, C55, C56, C57, C58, C59, C60, C61, C62, C63, C64, C65, C66, C67, C68, C69, C70, C71, C72, C73, C74, C75, C76, C77, C78, C79, C80: 4.7uF 100V; C_1206_3216Metric; MPN GRJ31CC72A475KE01K

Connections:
GNDPWR: C45.2, C46.2, C47.2, C48.2, C49.2, C50.2, C51.2, C52.2, C53.2, C54.2, C55.2, C56.2, C57.2, C58.2, C59.2, C60.2, C61.2, C62.2, C63.2, C64.2, C65.2, C66.2, C67.2, C68.2, C69.2, C70.2, C71.2, C72.2, C73.2, C74.2, C75.2, C76.2, C77.2, C78.2, C79.2, C80.2; also elsewhere on the board
V+: C45.1, C46.1, C47.1, C48.1, C49.1, C50.1, C51.1, C52.1, C53.1, C54.1, C55.1, C56.1, C57.1, C58.1, C59.1, C60.1, C61.1, C62.1, C63.1, C64.1, C65.1, C66.1, C67.1, C68.1, C69.1, C70.1, C71.1, C72.1, C73.1, C74.1, C75.1, C76.1, C77.1, C78.1, C79.1, C80.1; also elsewhere on the board


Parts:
C81: 0.1uF; C_0402_1005Metric; MPN MF-CAP-0402-0.1uF
J3: SM06B-GHS-TB; CONN_SM06B-GHS-TB_JST; MPN SM06B-GHS-TB(LF)(SN)
R41, R42: 120; R_0402_1005Metric; MPN RC0402FR-07120RL
U8: SN65HVD35DR; D14; MPN SN65HVD35DR

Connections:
+3V: C81.1, U8.13 (VCC), U8.14 (VCC); also elsewhere on the board
+5V: J3.1; also elsewhere on the board
/aux1/AUX1_D: U8.2 (R); also elsewhere on the board
/aux1/AUX1_E: U8.5 (D); also elsewhere on the board
/rs422/RS422_DE: U8.4 (DE); also elsewhere on the board
/rs422/RS422_RE: U8.3 (*RE); also elsewhere on the board
/rs422/RS422_RX_N: J3.3, R41.2, U8.11 (B)
/rs422/RS422_RX_P: J3.2, R41.1, U8.12 (A)
/rs422/RS422_TX_N: J3.5, R42.2, U8.10 (Z)
/rs422/RS422_TX_P: J3.4, R42.1, U8.9 (Y)
GND: C81.2, J3.6, U8.6 (GND), U8.7 (GND); also elsewhere on the board


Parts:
AUX2: SM07B-GHS-TB(LF)(SN); JST_SM07B-GHS-TB(LF)(SN); MPN SM07B-GHS-TB(LF)(SN)
AUX2H1: Conn_02x04_Odd_Even; PinHeader_2x04_P1.27mm_Vertical
C35, C36: 1uF; C_0402_1005Metric; MPN MF-CAP-0402-1uF
C37, C38, C39, C40: DNP; C_0402_1005Metric; not fitted
D7, D8: BAT41KFILM; SOD-523_STM; MPN BAT41KFILM
R26, R27, R28, R30: 100; R_0402_1005Metric; MPN MF-RES-0402-100
R29, R31: 2k; R_0402_1005Metric; MPN MF-RES-0402-2K

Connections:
+3V: AUX2.2, AUX2H1.4, C36.1; also elsewhere on the board
+5V: AUX2.1, AUX2H1.2, C35.1; also elsewhere on the board
/aux2/AUX2P_A: AUX2.3, AUX2H1.7, AUX2H1.8, R26.1
/aux2/AUX2P_B: AUX2.4, AUX2H1.5, R27.1
/aux2/AUX2P_C: AUX2.5, AUX2H1.3, R28.1
/aux2/AUX2P_D: AUX2.6, AUX2H1.1, R30.1
/aux2/AUX2_A: C40.1, R26.2; also elsewhere on the board
/aux2/AUX2_B: C39.1, R27.2, R29.2; also elsewhere on the board
/aux2/AUX2_C: C38.1, R28.2, R31.2; also elsewhere on the board
/aux2/AUX2_D: C37.1, R30.2; also elsewhere on the board
/aux2/AUX2_I2C_PULLUP: D7.2, D8.2; also elsewhere on the board
GND: AUX2.7, AUX2H1.6, C35.2, C36.2, C37.2, C38.2, C39.2, C40.2; also elsewhere on the board
unnamed: D7.1, R29.1
unnamed: D8.1, R31.1

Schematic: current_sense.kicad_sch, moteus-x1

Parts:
C27, C28, C29: 1000pF; C_0402_1005Metric; MPN MF-CAP-0402-1nF
R17, R18, R19: 22; R_0402_1005Metric; MPN MF-RES-0402-22

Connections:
/Current Sense/CUR1: R17.1; also elsewhere on the board
/Current Sense/CUR2: R18.1; also elsewhere on the board
/Current Sense/CUR3: R19.1; also elsewhere on the board
/Current Sense/FCUR1: C27.1, R17.2; also elsewhere on the board
/Current Sense/FCUR2: C28.1, R18.2; also elsewhere on the board
/Current Sense/FCUR3: C29.1, R19.2; also elsewhere on the board
GND: C27.2, C28.2, C29.2; also elsewhere on the board

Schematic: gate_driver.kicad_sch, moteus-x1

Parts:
C18: 1uF; C_0603_1608Metric; MPN MF-CAP-0603-1uF
C19: 0.1uF 100V; C_0603_1608Metric; MPN GCJ188R72A104KA01D
C20: 1uF; C_0402_1005Metric; MPN MF-CAP-0402-1uF
C21: 1uF 25V; C_0603_1608Metric; MPN C1608X7R1E105K080AE
C22: 47nF 100V; C_0603_1608Metric; MPN C0603X473K1RAC7867
C23: 1uF; C_0603_1608Metric; MPN C1608X7R1E105K080AE
R12, R13: 2k; R_0402_1005Metric; MPN MF-RES-0402-2K
U5: DRV8353SRTAR; RTA0040B; MPN DRV8353SRTAR

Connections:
+3V: C18.2, R12.1, R13.1, U5.24 (VREF); also elsewhere on the board
+12V: C19.2, U5.3 (VM); also elsewhere on the board
/Current Sense/CUR1: U5.21 (SOC); also elsewhere on the board
/Current Sense/CUR2: U5.22 (SOB); also elsewhere on the board
/Current Sense/CUR3: U5.23 (SOA); also elsewhere on the board
/Gate Driver/CPH: C22.2, U5.2 (CPH)
/Gate Driver/CPL: C22.1, U5.1 (CPL)
/Gate Driver/DRV8323_CS: U5.30 (SCS_N); also elsewhere on the board
/Gate Driver/DRV8323_FAULT: R13.2, U5.26 (FAULT_N); also elsewhere on the board
/Gate Driver/DRV8323_MISO: R12.2, U5.27 (SDO); also elsewhere on the board
/Gate Driver/DRV8323_MOSI: U5.28 (SDI); also elsewhere on the board
/Gate Driver/DRV8323_SCLK: U5.29 (SCLK); also elsewhere on the board
/Gate Driver/GHA: U5.6 (GHA); also elsewhere on the board
/Gate Driver/GHB: U5.15 (GHB); also elsewhere on the board
/Gate Driver/GHC: U5.16 (GHC); also elsewhere on the board
/Gate Driver/GLA: U5.8 (GLA); also elsewhere on the board
/Gate Driver/GLB: U5.13 (GLB); also elsewhere on the board
/Gate Driver/GLC: U5.18 (GLC); also elsewhere on the board
/Gate Driver/MOTOR1: U5.32 (INHA); also elsewhere on the board
/Gate Driver/MOTOR2: U5.34 (INHB); also elsewhere on the board
/Gate Driver/MOTOR3: U5.36 (INHC); also elsewhere on the board
/Gate Driver/MOTOR_ENABLE: U5.31 (ENABLE); also elsewhere on the board
/Gate Driver/MOTOR_HIZ: U5.33 (INLA), U5.35 (INLB), U5.37 (INLC); also elsewhere on the board
/H Bridge A/OUTX: U5.7 (SHA); also elsewhere on the board
/H Bridge A/SXX_N: U5.10 (SNA); also elsewhere on the board
/H Bridge A/SXX_P: U5.9 (SPA); also elsewhere on the board
/H Bridge B/OUTX: U5.14 (SHB); also elsewhere on the board
/H Bridge B/SXX_N: U5.11 (SNB); also elsewhere on the board
/H Bridge B/SXX_P: U5.12 (SPB); also elsewhere on the board
/H Bridge C/OUTX: U5.17 (SHC); also elsewhere on the board
/H Bridge C/SXX_N: U5.20 (SNC); also elsewhere on the board
/H Bridge C/SXX_P: U5.19 (SPC); also elsewhere on the board
GND: C18.1, C20.1, C23.1, U5.25 (AGND); also elsewhere on the board
GNDPWR: C19.1, U5.39 (PGND), U5.41 (PAD); also elsewhere on the board
unnamed: C20.2, U5.38 (DVDD)
unnamed: C21.2, U5.5 (VCP)
unnamed: C23.2, U5.40 (VGLS)
V+: C21.1, U5.4 (VDRAIN); also elsewhere on the board

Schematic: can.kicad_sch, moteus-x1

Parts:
C30, C31: 0.1uF; C_0402_1005Metric; MPN MF-CAP-0402-0.1uF
CAN1, CAN2: S3B-PH-SM4-TB(LF)(SN); JST_S3B-PH-SM4-TB(LF)(SN); MPN S3B-PH-SM4-TB(LF)(SN)
CAN_DBG1: Conn_01x03_Pin; PinHeader_1x03_P2.00mm_Vertical
R20: 120; R_0603_1608Metric; not fitted
U6: TCAN1057AEV-Q1; SOIC-8_3.9x4.9mm_P1.27mm; MPN TCAN1057AEVDRQ1

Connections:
+3V: C30.1, U6.5 (VIO); also elsewhere on the board
+5V: C31.1, U6.3 (VCC); also elsewhere on the board
/CAN/CAN_N: CAN1.2, CAN2.2, CAN_DBG1.2, R20.2, U6.6 (CANL)
/CAN/CAN_P: CAN1.1, CAN2.1, CAN_DBG1.1, R20.1, U6.7 (CANH)
/CAN/CAN_RX: U6.4 (RXD); also elsewhere on the board
/CAN/CAN_TX: U6.1 (TXD); also elsewhere on the board
GND: C30.2, C31.2, CAN1.3, CAN2.3, CAN_DBG1.3, U6.2 (GND), U6.8 (STB), U6.9 (PAD); also elsewhere on the board

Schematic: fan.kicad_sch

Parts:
C82: 4.7uF; C_1206_3216Metric; MPN GRJ31CC72A475KE01K
FAN1: Conn_01x04_Pin; PinSocket_2x02_P2.54mm_Vertical
R43, R44: 100; R_0402_1005Metric; MPN MF-RES-0402-100

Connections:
+12V: C82.1, FAN1.2; also elsewhere on the board
/aux2/AUX2_C: R43.1; also elsewhere on the board
/aux2/AUX2_D: R44.1; also elsewhere on the board
GND: C82.2, FAN1.1; also elsewhere on the board
unnamed: FAN1.3, R44.2
unnamed: FAN1.4, R43.2

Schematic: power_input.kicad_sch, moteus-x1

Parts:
C1: 1uF 100V; C_0805_2012Metric; MPN GCM21BC72A105KE36L
C2: 0.1uF 100V; C_0603_1608Metric; MPN GCJ188R72A104KA01D
C3, C6: 1uF; C_0402_1005Metric; MPN MF-CAP-0402-1uF
C4, C7, C9: 22uF; C_1210_3225Metric; MPN GRM32ER71E226KE15L
C5: 5600pF; C_0402_1005Metric; MPN GCM155R71E562KA37D
C8: DNP; C_0402_1005Metric; not fitted
D3: SMBJ51D-M3/I; D_SMB; MPN SMBJ51D-M3/I
D13: US1B; D_SMA; MPN STPS1H100A
J1: XT30PW-M; AMASS_XT30PW-M; MPN XT30PW-M
J4: Conn_01x02_Pin; PinHeader_1x02_P2.00mm_Vertical
L1, L3: 2.2uH; IND_DFE252012_MUR; MPN DFE252012PD-2R2M=P2
L2: 100uH; IND_6028-WE-LQS_WRE; MPN 74404063101
M1, M2, M3, M4: Conn_01x01_Pin; M3_MOUNT_CORNER
NT1: NetTie_2; NetTie-2_SMD_Pad0.254mm
R1: 42.2k 1%; R_0402_1005Metric; MPN RC0402FR-0742K2L
R2: 69.8k 1%; R_0402_1005Metric; MPN RC0402FR-0769K8L
R3: 80.6k 1%; R_0402_1005Metric; MPN RC0402FR-0780K6L
R4: 22; R_0402_1005Metric; MPN MF-RES-0402-22
R5: 52.3k 1%; R_0402_1005Metric; MPN RC0402FR-0752K3L
R6: 226k 1%; R_0402_1005Metric; MPN RC0402FR-07226KL
R7: 16.2k 1%; R_0402_1005Metric; MPN RC0402FR-0716K2L
R8: DNP; R_0402_1005Metric; not fitted
TP1, TP2, TP3: TestPoint; TestPoint_THTPad_D1.5mm_Drill0.7mm
U1: MAX17760ATC+; 21-0664E_1233-1C_MXM; MPN MAX17760ATC+
U2, U3: TPS629203DRLR; SOT-5x3_DRL0008A_TEX; MPN TPS629203DRLR
VN1: Conn_01x01; POWER_M2.5
VP1: Conn_01x01; POWER_M2.5

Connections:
+3V: C9.1, L3.1, TP3.1, U3.3 (VOS); also elsewhere on the board
+5V: C4.1, D13.1 (K), L1.1, TP1.1, U2.3 (VOS), U3.6 (VIN), U3.7 (EN); also elsewhere on the board
+12V: C7.1, L2.1, R4.2, R6.1, TP2.1, U2.6 (VIN), U2.7 (EN); also elsewhere on the board
/Power Input/5V_IN: D13.2 (A), J4.1
GND: C4.2, C6.2, C7.2, C9.2, J4.2, NT1.2, R1.2, R3.2, R5.2, R7.2, U2.5 (GND), U3.5 (GND); also elsewhere on the board
GNDPWR: C1.2, C2.2, C3.2, C5.2, C8.2, D3.2 (A2), J1.N, NT1.1, R2.2, R8.2, U1.2 (PGND), U1.10 (MODE), U1.11 (SGND), U1.13 (EPAD), VN1.1; also elsewhere on the board
MOUNT_GND: C8.1, M4.1, R8.1
unnamed: C6.1, R4.1, U1.7 (EXTVCC)
unnamed: R6.2, R7.1, U1.8 (FB)
unnamed: L2.2, U1.12 (LX)
unnamed: R2.1, U1.6 (RT/SYNC)
unnamed: C5.1, U1.9 (SS)
unnamed: C3.1, U1.3 (VCC)
unnamed: R3.1, U2.1 (FB/VSET)
unnamed: R1.1, U2.8 (MODE/S-CONF)
unnamed: L1.2, U2.4 (SW)
unnamed: R5.1, U3.8 (MODE/S-CONF)
unnamed: L3.2, U3.4 (SW)
V+: C1.1, C2.1, D3.1 (A1), J1.P, U1.1 (VIN), VP1.1; also elsewhere on the board

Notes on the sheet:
FB: VSET FSW: 2.5MHz Output Discharge: No Mode: Auto PFM
FB: VSET FSW: 2.5MHz Output Discharge: No Mode: FPWM
0.9ms soft start
OPEN = 3.3V
400kHz

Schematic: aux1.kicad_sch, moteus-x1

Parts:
AUX1: SM08B-GHS-TB; CONN_SM08B-GHS-TB_JST; MPN SM08B-GHS-TB(LF)(SN)
AUX1_S1: Conn_01x04; PinHeader_1x04_P1.27mm_Vertical
C41, C42, C43: 1uF; C_0402_1005Metric; MPN MF-CAP-0402-1uF
C44: 0.1uF; C_0402_1005Metric; MPN MF-CAP-0402-0.1uF
D9, D10: BAT41KFILM; SOD-523_STM; MPN BAT41KFILM
R32, R33, R34, R35, R36: 100; R_0402_1005Metric; MPN MF-RES-0402-100
R37, R38: 2k; R_0402_1005Metric; MPN MF-RES-0402-2K
U7: MA600; QFN-16-1EP_3x3mm_P0.5mm_EP1.75x1.75mm; MPN MA600GQE-0000

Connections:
+3V: AUX1.2, AUX1_S1.1, C42.1, C43.1, C44.1, U7.13 (VDD), U7.14 (AVDD); also elsewhere on the board
+5V: AUX1.1, C41.1; also elsewhere on the board
/aux1/AS5047_CS: U7.5 (~CS); also elsewhere on the board
/aux1/AUX1P_A: AUX1.3, R32.1
/aux1/AUX1P_B: AUX1.4, R33.1
/aux1/AUX1P_C: AUX1.5, R34.1
/aux1/AUX1P_D: AUX1.6, AUX1_S1.2, R35.1
/aux1/AUX1P_E: AUX1.7, AUX1_S1.3, R36.1
/aux1/AUX1_A: R32.2, U7.12 (SCLK); also elsewhere on the board
/aux1/AUX1_B: R33.2, U7.7 (MISO); also elsewhere on the board
/aux1/AUX1_C: R34.2, U7.4 (MOSI); also elsewhere on the board
/aux1/AUX1_D: R35.2, R37.2; also elsewhere on the board
/aux1/AUX1_E: R36.2, R38.2; also elsewhere on the board
/aux1/AUX1_I2C_PULLUP: D9.2, D10.2; also elsewhere on the board
GND: AUX1.8, AUX1_S1.4, C41.2, C42.2, C43.2, C44.2, U7.8 (GND), U7.10 (TEST); also elsewhere on the board
unnamed: D9.1, R37.1
unnamed: D10.1, R38.1



Board: 6 copper layers, 56.0 x 56.0 mm, 187 parts (108 on the bottom side), 106 nets.

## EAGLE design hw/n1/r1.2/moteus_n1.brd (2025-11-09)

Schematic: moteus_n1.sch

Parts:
A: PAD16AWG_TERM; 16AWG_TERM
AUX1: SM08B-GHS-TB(LF)(SN); JST_SM08B-GHS-TB(LF)(SN); MPN SM08B-GHS-TB(LF)(SN)
AUX2: SM07B-GHS-TB(LF)(SN); JST_SM07B-GHS-TB(LF)(SN); MPN SM07B-GHS-TB(LF)(SN)
B: PAD16AWG_TERM; 16AWG_TERM
C: PAD16AWG_TERM; 16AWG_TERM
C1, C19, C20, C21, C22, C25, C26, C27, C28, C29: DNP; C0402
C2: 1uF 100V; C0805; MPN GCM21BC72A105KE36L
C3, C17, C18, C23\, C24: 1uF; C0603; MPN MF-CAP-0603-1uF
C4, C13: 10uF; C1206; MPN MF-CAP-1206-10uF
C5, C10, C38, C40, C41: 1uF; C0402; MPN MF-CAP-0402-1uF
C6: 22uF; C1206; MPN CL31B226KPHNNNE
C7, C8, C9, C11, C12, C14, C15, C16, C30, C32, C33, C42: 0.1uF; C0402; MPN MF-CAP-0402-0.1uF
C31: 0.01uF; C0402; MPN MF-CAP-0402-0.01uF
C34, C35, C36: 1000pF; C0402; MPN MF-CAP-0402-1nF
C37, C39: 0.1uF 100V; C0603; MPN GCJ188R72A104KA01D
C43: 0.47uF 100V; C0805; MPN 08051C474KAT2A
C44, C45, C46: 0.1uF 100V; C1206; MPN 12061C104KAT2A
C47, C48: 4.7uF 100V; C1206; MPN GRJ31CC72A475KE01K
C49, C50, C51, C52, C53, C54, C55, C56, C57, C58, C59, C60, C61, C62, C63, C64, C65, C66, C67, C68, C69, C70, C71, C72, C73, C74, C75, C76, C77, C78, C79, C80, C81, C82, C83, C84, C85, C86: 4.7uF 100V; C1206_NOBORDER; MPN GRJ31CC72A475KE01K
CAN1, CAN2: JST-PH3; JST_S3B-PH-SM4-TB(LF)(SN); MPN S3B-PH-SM4-TB(LF)(SN)
CANG: PAD24AWG_PAD; 24AWG_PAD
CANH: PAD24AWG_PAD; 24AWG_PAD
CANL: PAD24AWG_PAD; 24AWG_PAD
D1: MF-LED-0603-RED; LED0603
D2: MF-LED-0603-RED; LED0603; MPN MF-LED-0603-GREEN
D3, D4, D5, D6, D7, D8, D9, D10, D11: BAT41KFILM; SODFL1608X70N; MPN BAT41KFILM
D12: DIODE-DO214AA; DO214AA; MPN SMBJ51D-M3/I
D33, D50: PAD24AWG_PAD; 24AWG_PAD
DAC: PAD24AWG_PAD; 24AWG_PAD
DG1: PAD24AWG_PAD; 24AWG_PAD
DTR: PAD24AWG_PAD; 24AWG_PAD
DTX: PAD24AWG_PAD; 24AWG_PAD
J1, J2: XT30XT30PW_MALE; XT30PW_MALE; MPN XT30PW-M
J3: SM06B-GHS-TB(LF)(SN); JST_SM06B-GHS-TB(LF)(SN); MPN SM06B-GHS-TB(LF)(SN)
L1: SRN4018-220M; IND_BOURNS_SRN4018; MANUFACTURER_PART_NUMBER 74404042470
L2: 74404024100; IND_4024100_WRE; MPN 74404024100
M1, M2, M3, M4: MOUNT; M2.5MOUNT
Q1, Q3, Q5: TPH1R204PL_VIAS; SOP_ADVANCE_8_VIAS; MPN TPH2R408QM,L1Q
Q2, Q4, Q6: TPH1R204PLSOP_ADVANCE_8; SOP_ADVANCE_8; MPN TPH2R408QM,L1Q
R1, R2: DNP; R0402
R3, R15: 100k 1%; R0402; MPN RC0402FR-07100KL
R4, R5, R8, R9, R10, R11, R12, R13, R14: 100; R0402; MPN MF-RES-0402-100
R6, R7, R25, R26, R33, R34: 2k; R0402; MPN MF-RES-0402-2K
R16: 4.7k 1%; R0402; MPN RC0402FR-074K7L
R17: 47k NTC; R0402; MPN NCP15WB473F03RC
R18, R19: 10k 1%; R0402; MPN RC0402FR-0710KL
R20, R21: 560; R0402; MPN MF-RES-0402-560
R22, R23, R24: 22; R0402; MPN MF-RES-0402-22
R27, R28, R30, R31, R32: 7.5; R0402; MPN RC0402FR-077R5L
R29: 7.5; R0805; MPN RC0805FR-077R5L
R35, R36: 120; R0402; MPN RC0402FR-07120RL
R37: DNP; R0805
RA: 0.5mOhm 1% 2W; M1206; MPN HCS1206FTL500
RB: 0.5mOhm 1% 2W; M1206; MPN HCS1206FTL500
RC: 0.5mOhm 1% 2W; M1206; MPN HCS1206FTL500
SH1, SH2, SH3: SHORTT5; SHORT_TOP-50
SH4: SHORTMEDIUM; SHORT_TOP-MEDIUM
SWD: JST-ZH6; JST_S6B-ZR-SM4A-TF(LF)(SN); MPN S6B-ZR-SM4A-TF(LF)(SN)
TEMP1, TEMP2: PAD24AWG_PAD; 24AWG_PAD
U1: MAX15062AATA+T; 21-0487A_MXM; MANUFACTURER_PART_NUMBER MAX15062BATA+T
U2: XC9265A331MR-G; SOT95P280X130-5N; MPN XC9265A331MR-G
U3: STM32G474CEU6; QFN50P700X700X60-49N; MPN STM32G474CEU6
U4: TCAN1042HGV; SOIC8; MPN TCAN1057AEVDRQ1
U5: AS5147; TSSOP14; MPN AS5047P-ATSM
U7: DRV8353S; WQFN-40; MPN DRV8353FSRTAR
U8: SN65HVD35DR; D14
VN: PAD16AWG_TERM; 16AWG_TERM
VP: PAD16AWG_TERM; 16AWG_TERM

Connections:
+3V3: AUX1.2, AUX2.2, C6.P$1, C7.P$1, C8.P$1, C10.P$1, C11.P$1, C12.P$1, C13.P$2, C15.P$1, C16.P$1, C18.P$1, C24.P$1, C30.P$1, C42.P$2, D33.P$1, L2.1, R2.P$2, R17.P$1, R20.P$1, R21.P$1, R25.P$1, R26.P$1, SWD.6, TEMP1.P$1, U2.4 (VOUT), U3.1 (VBAT), U3.20 (VREF+), U3.21 (VDDA), U3.23 (VDD_1), U3.35 (VDD_2), U3.48 (VDD_3), U4.5 (VIO), U5.12 (VDD3V), U7.24 (VREF), U8.13 (VCC_2), U8.14 (VCC)
+5V: AUX1.1, AUX2.1, C4.P$1, C5.P$1, C14.P$1, C17.P$1, C23\.P$1, D50.P$1, J3.1, L1.1, U1.4 (FB/VOUT), U2.1 (VIN), U2.3 (CE), U4.3 (VCC)
AS5047_CS: U3.19 (PB2), U5.1 (CS/)
AUX1_A: C29.P$1, R10.P$2, U3.13 (PA5), U3.27 (PB14), U5.2 (CLK)
AUX1_B: C28.P$1, R11.P$2, U3.42 (PB4), U5.3 (MISO)
AUX1_C: C27.P$1, R12.P$2, U3.15 (PA7), U5.4 (MOSI)
AUX1_D: C26.P$1, DTR.P$1, R13.P$2, R34.P$2, U3.38 (PA15), U8.2 (R)
AUX1_E: C25.P$1, DTX.P$1, R14.P$2, R33.P$2, U3.41 (PB3), U3.47 (PB9), U8.5 (D)
AUX1_I2C_PULLUP: R33.P$1, R34.P$1, U3.46 (PB8-BOOT0)
AUX2_A: C22.P$1, R4.P$2, U3.6 (PF1-OSC_OUT)
AUX2_B: C21.P$1, R5.P$2, R6.P$2, U3.5 (PF0-OSC_IN), U3.32 (PA10)
AUX2_C: C20.P$1, R7.P$2, R9.P$2, U3.16 (PC4), U3.33 (PA11)
AUX2_D: C19.P$1, R8.P$2, U3.45 (PB7)
AUX2_I2C_PULLUP: R6.P$1, R7.P$1, U3.34 (PA12)
CAN_N: CAN1.2, CAN2.2, CANL.P$1, R37.P$2, U4.6 (CANL)
CAN_P: CAN1.1, CAN2.1, CANH.P$1, R37.P$1, U4.7 (CANH)
CAN_RX: U3.43 (PB5), U4.4 (RXD)
CAN_TX: U3.44 (PB6), U4.1 (TXD)
CUR1: R22.P$1, U7.23 (SOA)
CUR2: R23.P$1, U7.22 (SOB)
CUR3: R24.P$1, U7.21 (SOC)
DAC: DAC.P$1, R2.P$1, R3.P$2, U3.12 (PA4)
DRV8323_CS: U3.17 (PB0), U7.30 (CS)
DRV8323_MISO: R25.P$2, U3.40 (PC11), U7.27 (MISO)
DRV8323_MOSI: U3.2 (PC13), U7.28 (MOSI)
DRV8323_SCLK: U3.39 (PC10), U7.29 (SCLK)
FCUR1: C34.P$1, R22.P$2, U3.11 (PA3)
FCUR2: C35.P$1, R23.P$2, U3.14 (PA6)
FCUR3: C36.P$1, R24.P$2, U3.18 (PB1)
GHA: D5.1 (K), R28.P$1, U7.6 (GHA)
GHA_D: D5.2 (A), Q1.4 (G), R28.P$2
GHB: D8.1 (K), R30.P$1, U7.15 (GHB)
GHB_D: D8.2 (A), Q3.4 (G), R30.P$2
GHC: D11.1 (K), R32.P$1, U7.16 (GHC)
GHC_D: D11.2 (A), Q5.4 (G), R32.P$2
GLA: D3.1 (K), R27.P$1, U7.8 (GLA)
GLA_D: D3.2 (A), D4.1 (K), Q2.4 (G), R27.P$2
GLB: D6.1 (K), R29.P$1, U7.13 (GLB)
GLB_D: D6.2 (A), D7.1 (K), Q4.4 (G), R29.P$2
GLC: D9.1 (K), R31.P$1, U7.18 (GLC)
GLC_D: D9.2 (A), D10.1 (K), Q6.4 (G), R31.P$2
GND: AUX1.8, AUX2.7, C3.P$2, C4.P$2, C5.P$2, C6.P$2, C7.P$2, C8.P$2, C9.P$2, C10.P$2, C11.P$2, C12.P$2, C13.P$1, C14.P$2, C15.P$2, C16.P$2, C17.P$2, C18.P$2, C19.P$2, C20.P$2, C21.P$2, C22.P$2, C23\.P$2, C24.P$2, C25.P$2, C26.P$2, C27.P$2, C28.P$2, C29.P$2, C30.P$2, C31.P$2, C32.P$2, C33.P$2, C34.P$2, C35.P$2, C36.P$2, C42.P$1, CAN1.3, CAN2.3, CANG.P$1, DG1.P$1, J3.6, R3.P$1, R16.P$1, R18.P$2, R19.P$2, SH4.2, SWD.4, U1.7 (GND), U2.2 (GND), U3.49 (THERMALPAD), U4.2 (GND), U4.8 (STB), U5.5 (TEST), U5.13 (GND), U7.25 (AGND), U8.6 (GND_2), U8.7 (GND)
LED1: D1.CATHODE, U3.28 (PB15)
LED2: D2.CATHODE, U3.29 (PC6)
MOTOR1: U3.8 (PA0), U7.32 (INHA)
MOTOR2: U3.9 (PA1), U7.34 (INHB)
MOTOR3: U3.10 (PA2), U7.36 (INHC)
MOTOR_ENABLE: U3.3 (PC14-OSC32_IN), U7.31 (ENABLE)
MOTOR_FAULT: R26.P$2, U3.26 (PB13), U7.26 (FAULT)
MOTOR_HIZ: U3.4 (PC15-OSC32_OUT), U7.33 (INLA), U7.35 (INLB), U7.37 (INLC)
unnamed: C1.P$1, M3.P$1, R1.P$1
unnamed: C40.P$2, U7.40 (VGLS)
unnamed: AUX2.3, R4.P$1
unnamed: C3.P$1, U1.3 (VCC)
unnamed: L2.2, U2.5 (LX)
unnamed: AUX2.4, R5.P$1
unnamed: AUX2.6, R8.P$1
unnamed: AUX2.5, R9.P$1
unnamed: AUX1.3, R10.P$1
unnamed: C39.P$2, U7.1 (CPL)
unnamed: AUX1.4, R11.P$1
unnamed: AUX1.5, R12.P$1
unnamed: C39.P$1, U7.2 (CPH)
unnamed: C38.P$2, U7.5 (VCP)
unnamed: AUX1.6, R13.P$1
unnamed: C41.P$2, U7.38 (DVDD)
unnamed: D1.ANODE, R20.P$2
unnamed: D2.ANODE, R21.P$2
unnamed: AUX1.7, R14.P$1
NRST: C9.P$1, SWD.2, U3.7 (PG10-NRST)
RS422_A: J3.2, R35.P$2, U8.12 (A)
RS422_B: J3.3, R35.P$1, U8.11 (B)
RS422_DE: U3.24 (PB11), U8.4 (DE)
RS422_RE: U3.22 (PB10), U8.3 (!RE)
RS422_Y: J3.4, R36.P$2, U8.9 (Y)
RS422_Z: J3.5, R36.P$1, U8.10 (Z)
SHA: A.1, A.2, A.3, A.4, A.5, A.6, A.7, A.8, A.9, A.10, A.11, A.12, Q1.1 (S), Q1.2 (S), Q1.3 (S), Q2.5 (D), Q2.6 (D), Q2.7 (D), Q2.8 (D), Q2.PAD (D), U7.7 (SHA)
SHB: B.1, B.2, B.3, B.4, B.5, B.6, B.7, B.8, B.9, B.10, B.11, B.12, Q3.1 (S), Q3.2 (S), Q3.3 (S), Q4.5 (D), Q4.6 (D), Q4.7 (D), Q4.8 (D), Q4.PAD (D), U7.14 (SHB)
SHC: C.1, C.2, C.3, C.4, C.5, C.6, C.7, C.8, C.9, C.10, C.11, C.12, Q5.1 (S), Q5.2 (S), Q5.3 (S), Q6.5 (D), Q6.6 (D), Q6.7 (D), Q6.8 (D), Q6.PAD (D), U7.17 (SHC)
SWCLK: SWD.5, U3.37 (PA14)
SWDIO: SWD.3, U3.36 (PA13)
SXA_N: SH1.1, U7.10 (SNA)
SXA_P: C44.P$2, Q2.1 (S), Q2.2 (S), Q2.3 (S), RA.2, U7.9 (SPA)
SXB_N: SH2.1, U7.11 (SNB)
SXB_P: C45.P$2, Q4.1 (S), Q4.2 (S), Q4.3 (S), RB.2, U7.12 (SPB)
SXC_N: SH3.1, U7.20 (SNC)
SXC_P: C46.P$2, Q6.1 (S), Q6.2 (S), Q6.3 (S), RC.2, U7.19 (SPC)
V+: C2.P$1, C37.P$1, C38.P$1, C43.P$1, C44.P$1, C45.P$1, C46.P$1, C47.P$1, C48.P$1, C49.P$1, C50.P$1, C51.P$1, C52.P$1, C53.P$1, C54.P$1, C55.P$1, C56.P$1, C57.P$1, C58.P$1, C59.P$1, C60.P$1, C61.P$1, C62.P$1, C63.P$1, C64.P$1, C65.P$1, C66.P$1, C67.P$1, C68.P$1, C69.P$1, C70.P$1, C71.P$1, C72.P$1, C73.P$1, C74.P$1, C75.P$1, C76.P$1, C77.P$1, C78.P$1, C79.P$1, C80.P$1, C81.P$1, C82.P$1, C83.P$1, C84.P$1, C85.P$1, C86.P$1, D12.C, J1.1, J2.1, Q1.5 (D), Q1.6 (D), Q1.7 (D), Q1.8 (D), Q1.PAD (D), Q3.5 (D), Q3.6 (D), Q3.7 (D), Q3.8 (D), Q3.PAD (D), Q5.5 (D), Q5.6 (D), Q5.7 (D), Q5.8 (D), Q5.PAD (D), R15.P$2, U1.1 (VIN), U1.2 (EN/UVLO), U7.3 (VM), U7.4 (VDRAIN), VP.1, VP.2, VP.3, VP.4, VP.5, VP.6, VP.7, VP.8, VP.9, VP.10, VP.11, VP.12
V-: C1.P$2, C2.P$2, C37.P$2, C40.P$1, C41.P$1, C43.P$2, C47.P$2, C48.P$2, C49.P$2, C50.P$2, C51.P$2, C52.P$2, C53.P$2, C54.P$2, C55.P$2, C56.P$2, C57.P$2, C58.P$2, C59.P$2, C60.P$2, C61.P$2, C62.P$2, C63.P$2, C64.P$2, C65.P$2, C66.P$2, C67.P$2, C68.P$2, C69.P$2, C70.P$2, C71.P$2, C72.P$2, C73.P$2, C74.P$2, C75.P$2, C76.P$2, C77.P$2, C78.P$2, C79.P$2, C80.P$2, C81.P$2, C82.P$2, C83.P$2, C84.P$2, C85.P$2, C86.P$2, D4.2 (A), D7.2 (A), D10.2 (A), D12.A, J1.2, J2.2, R1.P$2, RA.1, RB.1, RC.1, SH1.2, SH2.2, SH3.2, SH4.1, U7.39 (GND), U7.PAD, VN.1, VN.2, VN.3, VN.4, VN.5, VN.6, VN.7, VN.8, VN.9, VN.10, VN.11, VN.12
VBAT_SENSE: C31.P$1, R15.P$1, R16.P$2, U3.31 (PA9)
VSW: L1.2, U1.8 (LX)
VTEMP_FET: C32.P$1, R17.P$2, R18.P$1, U3.25 (PB12)
VTEMP_MOT: C33.P$1, R19.P$1, TEMP2.P$1, U3.30 (PA8)

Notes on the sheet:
PCB rev divider HI / LO r1.1 - open / 100k



Board: 4 copper layers, 46.0 x 46.0 mm, 185 parts (107 on the bottom side), 93 nets.

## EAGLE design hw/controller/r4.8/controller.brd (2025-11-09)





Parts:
A: PAD16AWG_PAD; 16AWG_PAD
ABS: JST_ZH4; JST_S4B-ZR-SM4A-TF(LF)(SN); MPN S4B-ZR-SM4A-TF(LF)(SN)
B: PAD16AWG_PAD; 16AWG_PAD
C: PAD16AWG_PAD; 16AWG_PAD
C1, C2, C3, C5, C6, C8, C10, C11, C12, C13, C18: 0.1uF; C0402; MPN MF-CAP-0402-0.1uF
C4, C9, C15, C17, C38, C56: 1uF; C0402; MPN MF-CAP-0402-1uF
C7, C21: 10uF; C1206; MPN MF-CAP-1206-10uF
C14, C16: 0.1uF 50V; C0402; MPN CGA2B3X7R1H104K050BB
C19: 0.47uF 50V; C0402; MPN GRM155R61H474KE11D
C20: 1uF; C0603; MPN MF-CAP-0603-1uF
C22, C23, C24, C25, C26, C27, C28, C29, C30, C31, C32, C33, C34, C36, C37: 10uF 50V; C1206; MPN C3216X7R1H106K160AE
C35: 10uF 50V; C1206_NOBORDER; MPN C3216X7R1H106K160AE
C39: 1uF 100V; C0805; MPN GCM21BC72A105KE36L
C40, C41, C42, C43, C44, C45, C46, C47, C48, C49, C50, C51, C52, C53, C54: DNP; C1206_NOCREAM
C55: DNP; C0402
C57: 0.01uF; C0402; MPN MF-CAP-0402-0.01uF
C58, C59, C60: 1000pF; C0402; MPN MF-CAP-0402-1nF
CAN1, CAN2: JST-PH3; JST_S3B-PH-SM4-TB(LF)(SN); MPN S3B-PH-SM4-TB(LF)(SN)
D2: MF-LED-0603-RED; LED0603; MPN MF-LED-0603-GREEN
D3: MF-LED-0603-RED; LED0603
D4: DUAL_TVS; SOT23-3; MPN CDSOT23-0502B
D33: PAD24AWG_PAD; 24AWG_PAD
DA: PAD24AWG_PAD; 24AWG_PAD
DAC: PAD24AWG_PAD; 24AWG_PAD
DB: PAD24AWG_PAD; 24AWG_PAD
DBG1, DBG2: PAD24AWG_PAD; 24AWG_PAD
DC: PAD24AWG_PAD; 24AWG_PAD
DG1, DG2: PAD24AWG_PAD; 24AWG_PAD
DRV_CS: PAD24AWG_PAD; 24AWG_PAD
DRV_MISO: PAD24AWG_PAD; 24AWG_PAD
DRV_MOSI: PAD24AWG_PAD; 24AWG_PAD
DRV_SCK: PAD24AWG_PAD; 24AWG_PAD
DTR: PAD24AWG_PAD; 24AWG_PAD
DTX: PAD24AWG_PAD; 24AWG_PAD
ENC: PICO-SPOX-6NOPASTE; PICO-SPOX-SMT-RA-6-NOPASTE
J1, J2: XT30XT30PW_MALE; XT30PW_MALE
L1: SRN4018-220M; IND_BOURNS_SRN4018; MANUFACTURER_PART_NUMBER SRN4018-330M
L2, L3: HALF_CHOKE; 1812_COMMON_HALF; MPN MF-RES-0805-0
M1, M2, M3, M4: MOUNT; M2.5MOUNT
MOT1, MOT2, MOT3: PAD24AWG_PAD; 24AWG_PAD
Q1, Q2, Q3, Q4, Q5, Q6: TPH1R204PLSOP_ADVANCE_8; SOP_ADVANCE_8; MPN TPH2R506PL,L1Q
R1, R2: 560; R0402; MPN MF-RES-0402-560
R3, R4, R13, R14: 2k; R0402; MPN MF-RES-0402-2K
R5: 100k 1%; R0402; MPN RC0402FR-07100KL
R6: 4.7k 1%; R0402; MPN RC0402FR-074K7L
R7, R9: 10k 1%; R0402; MPN RC0402FR-0710KL
R8: 47k NTC; R0402; MPN NCP15WB473F03RC
R10: DNP; R0402
R15, R16, R17: 22; R0402; MPN MF-RES-0402-22
RA: 0.5mOhm 1% 2W; M1206; MPN HCS1206FTL500
RB: 0.5mOhm 1% 2W; M1206; MPN HCS1206FTL500
RC: 0.5mOhm 1% 2W; M1206; MPN HCS1206FTL500
SH1, SH2, SH3: SHORTT5; SHORT_TOP-50
SH4: SHORTMEDIUM; SHORT_TOP-MEDIUM
SWD: JST-ZH6; JST_S6B-ZR-SM4A-TF(LF)(SN); MPN S6B-ZR-SM4A-TF(LF)(SN)
TEMP1, TEMP2: PAD24AWG_PAD; 24AWG_PAD
U1: STM32G474CEU6; QFN50P700X700X60-49N; MPN STM32G474CEU6
U2: TCAN334GSOT23; SOT23-8; MPN TCAN334GDCNT
U3: AS5147; TSSOP14; MPN AS5047P-ATSM
U4: MAX15062AATA+T; 21-0487A_MXM; MPN MAX15062AATA+T
U5: DRV8353S; WQFN-40; MPN DRV8353FSRTAR

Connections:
+3V3: ABS.1, C1.P$1, C2.P$1, C4.P$1, C5.P$1, C6.P$1, C7.P$2, C8.P$1, C9.P$1, C10.P$1, C11.P$1, C12.P$1, C18.P$2, C21.P$1, C56.P$1, D33.P$1, ENC.1, L1.1, R1.P$1, R2.P$1, R3.P$1, R4.P$1, R8.P$1, R13.P$1, R14.P$1, SWD.6, TEMP1.P$1, U1.1 (VBAT), U1.20 (VREF+), U1.21 (VDDA), U1.23 (VDD_1), U1.35 (VDD_2), U1.48 (VDD_3), U2.3 (VCC), U3.12 (VDD3V), U4.4 (FB/VOUT), U5.24 (VREF)
AS5047_A: U1.43 (PB5), U3.7 (A)
AS5047_B: U1.42 (PB4), U3.6 (B)
AS5047_CS: U1.24 (PB11), U3.1 (CS/)
AS5047_MISO: ENC.5, U1.27 (PB14), U3.3 (MISO)
AS5047_MOSI: ENC.6, U1.28 (PB15), U3.4 (MOSI)
AS5047_SCK: ENC.4, U1.26 (PB13), U3.2 (CLK)
CAN2_N: L2.P$2 (2), U2.6 (CANL)
CAN2_P: L3.P$2 (2), U2.7 (CANH)
CAN_N: CAN1.2, CAN2.2, D4.2, L2.P$1 (1)
CAN_P: CAN1.1, CAN2.1, D4.1, L3.P$1 (1)
CAN_RX: U1.33 (PA11), U2.4 (RXD)
CAN_TX: U1.34 (PA12), U2.1 (TXD)
CUR1: R15.P$1, U5.23 (SOA)
CUR2: R16.P$1, U5.22 (SOB)
CUR3: R17.P$1, U5.21 (SOC)
DAC: DAC.P$1, U1.12 (PA4)
DEBUG1: DBG1.P$1, U1.3 (PC14-OSC32_IN)
DEBUG2: DBG2.P$1, U1.4 (PC15-OSC32_OUT)
DEBUG_RX: DTR.P$1, U1.40 (PC11)
DEBUG_TX: DTX.P$1, U1.39 (PC10)
DRV8323_CS: DRV_CS.P$1, U1.16 (PC4), U5.30 (CS)
DRV8323_MISO: DRV_MISO.P$1, R13.P$2, U1.14 (PA6), U5.27 (MISO)
DRV8323_MOSI: DRV_MOSI.P$1, U1.15 (PA7), U5.28 (MOSI)
DRV8323_SCLK: DRV_SCK.P$1, U1.13 (PA5), U5.29 (SCLK)
FCUR1: C58.P$1, R15.P$2, U1.17 (PB0)
FCUR2: C59.P$1, R16.P$2, U1.18 (PB1)
FCUR3: C60.P$1, R17.P$2, U1.19 (PB2)
GHA: Q1.4 (G), U5.6 (GHA)
GHB: Q3.4 (G), U5.15 (GHB)
GHC: Q5.4 (G), U5.16 (GHC)
GLA: Q2.4 (G), U5.8 (GLA)
GLB: Q4.4 (G), U5.13 (GLB)
GLC: Q6.4 (G), U5.18 (GLC)
GND: ABS.4, C1.P$2, C2.P$2, C3.P$2, C4.P$2, C5.P$2, C6.P$2, C7.P$1, C8.P$2, C9.P$2, C10.P$2, C11.P$2, C12.P$2, C13.P$2, C18.P$1, C20.P$2, C21.P$2, C56.P$2, C57.P$2, C58.P$2, C59.P$2, C60.P$2, CAN1.3, CAN2.3, D4.3, DG1.P$1, DG2.P$1, ENC.3, R6.P$1, R7.P$2, R9.P$2, SH4.2, SWD.4, U1.29 (PC6), U1.38 (PA15), U1.49 (THERMALPAD), U2.2 (GND), U2.5 (SHDN), U2.8 (STB), U3.5 (TEST), U3.13 (GND), U4.7 (GND), U5.25 (AGND)
I2C_ABS_SCL: ABS.2, R4.P$2, U1.46 (PB8-BOOT0)
I2C_ABS_SDA: ABS.3, R3.P$2, U1.47 (PB9)
LED1: D3.CATHODE, U1.5 (PF0-OSC_IN)
LED2: D2.CATHODE, U1.6 (PF1-OSC_OUT)
MOTOR1: MOT1.P$1, U1.8 (PA0), U5.32 (INHA)
MOTOR2: MOT2.P$1, U1.9 (PA1), U5.34 (INHB)
MOTOR3: MOT3.P$1, U1.10 (PA2), U5.36 (INHC)
MOTOR_ENABLE: U1.11 (PA3), U5.31 (ENABLE)
MOTOR_FAULT: R14.P$2, U1.44 (PB6), U5.26 (FAULT)
MOTOR_HIZ: U1.45 (PB7), U5.33 (INLA), U5.35 (INLB), U5.37 (INLC)
unnamed: C55.P$1, M3.P$1, R10.P$1
unnamed: C38.P$2, U5.40 (VGLS)
unnamed: C20.P$1, U4.3 (VCC)
unnamed: C16.P$2, U5.1 (CPL)
unnamed: C16.P$1, U5.2 (CPH)
unnamed: C15.P$2, U5.5 (VCP)
unnamed: C17.P$2, U5.38 (DVDD)
unnamed: D3.ANODE, R1.P$2
unnamed: D2.ANODE, R2.P$2
NRST: C3.P$1, SWD.2, U1.7 (PG10-NRST)
SECONDARY_ENC_CS: ENC.2, U1.2 (PC13)
SHA: A.1, DA.P$1, Q1.1 (S), Q1.2 (S), Q1.3 (S), Q2.5 (D), Q2.6 (D), Q2.7 (D), Q2.8 (D), Q2.PAD (D), U5.7 (SHA)
SHB: B.1, DB.P$1, Q3.1 (S), Q3.2 (S), Q3.3 (S), Q4.5 (D), Q4.6 (D), Q4.7 (D), Q4.8 (D), Q4.PAD (D), U5.14 (SHB)
SHC: C.1, DC.P$1, Q5.1 (S), Q5.2 (S), Q5.3 (S), Q6.5 (D), Q6.6 (D), Q6.7 (D), Q6.8 (D), Q6.PAD (D), U5.17 (SHC)
SWCLK: SWD.5, U1.37 (PA14)
SWDIO: SWD.3, U1.36 (PA13)
SXA_N: SH1.1, U5.10 (SNA)
SXA_P: Q2.1 (S), Q2.2 (S), Q2.3 (S), RA.2, U5.9 (SPA)
SXB_N: SH2.1, U5.11 (SNB)
SXB_P: Q4.1 (S), Q4.2 (S), Q4.3 (S), RB.2, U5.12 (SPB)
SXC_N: SH3.1, U5.20 (SNC)
SXC_P: Q6.1 (S), Q6.2 (S), Q6.3 (S), RC.2, U5.19 (SPC)
V+: C14.P$1, C15.P$1, C19.P$1, C22.P$1, C23.P$1, C24.P$1, C25.P$1, C26.P$1, C27.P$1, C28.P$1, C29.P$1, C30.P$1, C31.P$1, C32.P$1, C33.P$1, C34.P$1, C35.P$1, C36.P$1, C37.P$1, C39.P$1, C40.P$1, C41.P$1, C42.P$1, C43.P$1, C44.P$1, C45.P$1, C46.P$1, C47.P$1, C48.P$1, C49.P$1, C50.P$1, C51.P$1, C52.P$1, C53.P$1, C54.P$1, J1.1, J2.1, Q1.5 (D), Q1.6 (D), Q1.7 (D), Q1.8 (D), Q1.PAD (D), Q3.5 (D), Q3.6 (D), Q3.7 (D), Q3.8 (D), Q3.PAD (D), Q5.5 (D), Q5.6 (D), Q5.7 (D), Q5.8 (D), Q5.PAD (D), R5.P$2, U4.1 (VIN), U4.2 (EN/UVLO), U5.3 (VM), U5.4 (VDRAIN)
V-: C14.P$2, C17.P$1, C19.P$2, C22.P$2, C23.P$2, C24.P$2, C25.P$2, C26.P$2, C27.P$2, C28.P$2, C29.P$2, C30.P$2, C31.P$2, C32.P$2, C33.P$2, C34.P$2, C35.P$2, C36.P$2, C37.P$2, C38.P$1, C39.P$2, C40.P$2, C41.P$2, C42.P$2, C43.P$2, C44.P$2, C45.P$2, C46.P$2, C47.P$2, C48.P$2, C49.P$2, C50.P$2, C51.P$2, C52.P$2, C53.P$2, C54.P$2, C55.P$2, J1.2, J2.2, R10.P$2, RA.1, RB.1, RC.1, SH1.2, SH2.2, SH3.2, SH4.1, U5.39 (GND), U5.P1 (PAD), U5.P2 (PAD), U5.P3 (PAD), U5.P7 (PAD), U5.P8 (PAD), U5.P9 (PAD), U5.P12 (PAD), U5.P13 (PAD), U5.P14 (PAD), U5.P17 (PAD), U5.P18 (PAD), U5.P19 (PAD), U5.PAD
VBAT_SENSE: C57.P$1, R5.P$1, R6.P$2, U1.25 (PB12)
VSW: L1.2, U4.8 (LX)
VTEMP_FET: C13.P$1, R8.P$2, R9.P$1, U1.31 (PA9)
VTEMP_MOT: R7.P$1, TEMP2.P$1, U1.30 (PA8)

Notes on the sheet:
PA10/PA15/PC6 Version 100
L2/L3 SIZED TO HOLD EITHER A) 2x 0805 0 OHM RESISTORS B) A COILCRAFT 1812CAN SERIES COMMON MODE CHOKE



Board: 4 copper layers, 46.0 x 53.0 mm, 133 parts (23 on the bottom side), 73 nets.

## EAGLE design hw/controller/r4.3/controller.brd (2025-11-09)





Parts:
A: PAD; 18AWG_PAD
ABS: JST_ZH4; JST_S4B-ZR-SM4A-TF(LF)(SN); MPN S4B-ZR-SM4A-TF(LF)(SN)
B: PAD; 18AWG_PAD
C: PAD; 18AWG_PAD
C1, C2, C3, C5, C6, C8, C10, C11, C12, C13, C18: 0.1uF; C0402; MPN MF-CAP-0402-0.1uF
C4, C9, C15, C17: 1uF; C0402; MPN MF-CAP-0402-1uF
C7, C21: 10uF; C1206; MPN MF-CAP-1206-10uF
C14, C16, C20: 0.1uF 50V; C0402; MPN CGA2B3X7R1H104K050BB
C19: 0.47uF 50V; C0402; MPN UMK105ABJ474KV-F
C22, C23, C24, C25, C26, C27, C28, C29, C30, C31, C32, C33, C34, C35, C36, C37: 10uF; C1206; MPN CGA5L1X7R1H106K160AC
CAN1, CAN2: JST-PH3; JST_S3B-PH-SM4-TB(LF)(SN); MPN S3B-PH-SM4-TB(LF)(SN)
D1: MF-DIO-SMA-B140; SMA
D2: MF-LED-0603-RED; LED0603; MPN MF-LED-0603-GREEN
D3: MF-LED-0603-RED; LED0603
D33: PAD24AWG_PAD; 24AWG_PAD
DA: PAD24AWG_PAD; 24AWG_PAD
DAC: PAD24AWG_PAD; 24AWG_PAD
DB: PAD24AWG_PAD; 24AWG_PAD
DBG1, DBG2: PAD24AWG_PAD; 24AWG_PAD
DC: PAD24AWG_PAD; 24AWG_PAD
DG1, DG2: PAD24AWG_PAD; 24AWG_PAD
DRV_CS: PAD24AWG_PAD; 24AWG_PAD
DRV_MISO: PAD24AWG_PAD; 24AWG_PAD
DRV_MOSI: PAD24AWG_PAD; 24AWG_PAD
DRV_SCK: PAD24AWG_PAD; 24AWG_PAD
DTR: PAD24AWG_PAD; 24AWG_PAD
DTX: PAD24AWG_PAD; 24AWG_PAD
J1, J2: XT30XT30PW_MALE; XT30PW_MALE
L1: SRN4018-220M; IND_BOURNS_SRN4018; MPN SRN4018-220M
M1, M2, M3, M4: MOUNT; M2.5MOUNT
MOT1, MOT2, MOT3: PAD24AWG_PAD; 24AWG_PAD
Q1, Q2, Q3, Q4, Q5, Q6: TPH1R204PLSOP_ADVANCE_8; SOP_ADVANCE_8; MPN TPH1R204PL,L1Q
R1, R2: 560; R0402; MPN MF-RES-0402-560
R3, R4, R13, R14: 2k; R0402; MPN MF-RES-0402-2K
R5, R10: 100k 1%; R0402; MPN ERJ-2RKF1003X
R6, R7, R9, R12: 10k 1%; R0402; MPN ERJ-2RKF1002X
R8: 47k NTC; R0402; MPN NCP15WB473F03RC
R11: 33k 1%; R0402; MPN ERJ-2RKF3302X
RA: 0.5mOhm 1% 2W; M1206; MPN HCS1206FTL500
RB: 0.5mOhm 1% 2W; M1206; MPN HCS1206FTL500
RC: 0.5mOhm 1% 2W; M1206; MPN HCS1206FTL500
SH1, SH2, SH3: SHORTT5; SHORT_TOP-50
SH4: SHORTBIG; SHORT_TOP-BIG
SWD: JST-ZH6; JST_S6B-ZR-SM4A-TF(LF)(SN); MPN S6B-ZR-SM4A-TF(LF)(SN)
TEMP1, TEMP2: PAD24AWG_PAD; 24AWG_PAD
U1: STM32G474CEU6; QFN50P700X700X60-49N; MPN STM32G474CEU6
U2: TCAN334GSOT23; SOT23-8; MPN TCAN334GDCNT
U3: AS5147; TSSOP14; MPN AS5047P-ATSM
U4: DRV8323RS; PVQFN-N48; MPN DRV8323RSRGZR

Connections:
+3V3: ABS.1, C1.P$1, C2.P$1, C4.P$1, C5.P$1, C6.P$1, C7.P$2, C8.P$1, C9.P$1, C10.P$1, C11.P$1, C12.P$1, C18.P$2, C21.P$1, D33.P$1, L1.1, R1.P$1, R2.P$1, R3.P$1, R4.P$1, R8.P$1, R11.P$1, R13.P$1, R14.P$1, SWD.6, TEMP1.P$1, U1.1 (VBAT), U1.20 (VREF+), U1.21 (VDDA), U1.23 (VDD_1), U1.35 (VDD_2), U1.48 (VDD_3), U2.3 (VCC), U3.12 (VDD3V), U4.26 (VREF)
AS5047_A: U1.43 (PB5), U3.7 (A)
AS5047_B: U1.42 (PB4), U3.6 (B)
AS5047_CS: U1.24 (PB11), U3.1 (CS/)
AS5047_MISO: U1.27 (PB14), U3.3 (MISO)
AS5047_MOSI: U1.28 (PB15), U3.4 (MOSI)
AS5047_SCK: U1.26 (PB13), U3.2 (CLK)
CAN_N: CAN1.2, CAN2.2, U2.6 (CANL)
CAN_P: CAN1.1, CAN2.1, U2.7 (CANH)
CAN_RX: U1.33 (PA11), U2.4 (RXD)
CAN_TX: U1.34 (PA12), U2.1 (TXD)
CUR1: U1.17 (PB0), U4.25 (SOA)
CUR2: U1.18 (PB1), U4.24 (SOB)
CUR3: U1.19 (PB2), U4.23 (SOC)
DAC: DAC.P$1, U1.12 (PA4)
DEBUG1: DBG1.P$1, U1.3 (PC14-OSC32_IN)
DEBUG2: DBG2.P$1, U1.4 (PC15-OSC32_OUT)
DEBUG_RX: DTR.P$1, U1.40 (PC11)
DEBUG_TX: DTX.P$1, U1.39 (PC10)
DRV8323_CS: DRV_CS.P$1, U1.16 (PC4), U4.32 (CS)
DRV8323_MISO: DRV_MISO.P$1, R13.P$2, U1.14 (PA6), U4.29 (MISO)
DRV8323_MOSI: DRV_MOSI.P$1, U1.15 (PA7), U4.30 (MOSI)
DRV8323_SCLK: DRV_SCK.P$1, U1.13 (PA5), U4.31 (SCLK)
GHA: Q1.4 (G), U4.8 (GHA)
GHB: Q3.4 (G), U4.17 (GHB)
GHC: Q5.4 (G), U4.18 (GHC)
GLA: Q2.4 (G), U4.10 (GLA)
GLB: Q4.4 (G), U4.15 (GLB)
GLC: Q6.4 (G), U4.20 (GLC)
GND: ABS.4, C1.P$2, C2.P$2, C3.P$2, C4.P$2, C5.P$2, C6.P$2, C7.P$1, C8.P$2, C9.P$2, C10.P$2, C11.P$2, C12.P$2, C13.P$2, C17.P$1, C18.P$1, C21.P$2, CAN1.3, CAN2.3, DG1.P$1, DG2.P$1, R6.P$1, R7.P$2, R9.P$2, SH4.2, SWD.4, U1.49 (THERMALPAD), U2.2 (GND), U2.5 (SHDN), U2.8 (STB), U3.5 (TEST), U3.13 (GND), U4.27 (DGND), U4.35 (AGND)
I2C_ABS_SCL: ABS.2, R4.P$2, U1.46 (PB8-BOOT0), U1.47 (PB9)
I2C_ABS_SDA: ABS.3, R3.P$2
LED1: D3.CATHODE, U1.5 (PF0-OSC_IN)
LED2: D2.CATHODE, U1.6 (PF1-OSC_OUT)
MOTOR1: MOT1.P$1, U1.8 (PA0), U4.37 (INHA)
MOTOR2: MOT2.P$1, U1.9 (PA1), U4.39 (INHB)
MOTOR3: MOT3.P$1, U1.10 (PA2), U4.41 (INHC)
MOTOR_ENABLE: U1.11 (PA3), U4.33 (ENABLE)
MOTOR_FAULT: R14.P$2, U1.44 (PB6), U4.28 (FAULT)
MOTOR_HIZ: U1.45 (PB7), U4.38 (INLA), U4.40 (INLB), U4.42 (INLC)
unnamed: R10.P$1, U4.48 (SHDN)
unnamed: R11.P$2, R12.P$1, U4.1 (FB)
unnamed: C16.P$2, U4.3 (CPL)
unnamed: C20.P$2, D1.CATHODE, L1.2, U4.45 (SW)
unnamed: C20.P$1, U4.44 (CB)
unnamed: C16.P$1, U4.4 (CPH)
unnamed: C15.P$2, U4.5 (VCP)
unnamed: C17.P$2, U4.36 (DVDD)
unnamed: D3.ANODE, R1.P$2
unnamed: D2.ANODE, R2.P$2
NRST: C3.P$1, SWD.2, U1.7 (PG10-NRST)
SHA: A.1, DA.P$1, Q1.1 (S), Q1.2 (S), Q1.3 (S), Q2.5 (D), Q2.6 (D), Q2.7 (D), Q2.8 (D), Q2.PAD (D), U4.9 (SHA)
SHB: B.1, DB.P$1, Q3.1 (S), Q3.2 (S), Q3.3 (S), Q4.5 (D), Q4.6 (D), Q4.7 (D), Q4.8 (D), Q4.PAD (D), U4.16 (SHB)
SHC: C.1, DC.P$1, Q5.1 (S), Q5.2 (S), Q5.3 (S), Q6.5 (D), Q6.6 (D), Q6.7 (D), Q6.8 (D), Q6.PAD (D), U4.19 (SHC)
SNA: SH1.1, U4.12 (SNA)
SNB: SH2.1, U4.13 (SNB)
SNC: SH3.1, U4.22 (SNC)
SPA: Q2.1 (S), Q2.2 (S), Q2.3 (S), RA.2, U4.11 (SPA)
SPB: Q4.1 (S), Q4.2 (S), Q4.3 (S), RB.2, U4.14 (SPB)
SPC: Q6.1 (S), Q6.2 (S), Q6.3 (S), RC.2, U4.21 (SPC)
SWCLK: SWD.5, U1.37 (PA14)
SWDIO: SWD.3, U1.36 (PA13)
V+: C14.P$1, C15.P$1, C19.P$1, C22.P$1, C23.P$1, C24.P$1, C25.P$1, C26.P$1, C27.P$1, C28.P$1, C29.P$1, C30.P$1, C31.P$1, C32.P$1, C33.P$1, C34.P$1, C35.P$1, C36.P$1, C37.P$1, J1.1, J2.1, Q1.5 (D), Q1.6 (D), Q1.7 (D), Q1.8 (D), Q1.PAD (D), Q3.5 (D), Q3.6 (D), Q3.7 (D), Q3.8 (D), Q3.PAD (D), Q5.5 (D), Q5.6 (D), Q5.7 (D), Q5.8 (D), Q5.PAD (D), R5.P$2, R10.P$2, U4.6 (VM), U4.7 (VDRAIN), U4.47 (VIN)
V-: C14.P$2, C19.P$2, C22.P$2, C23.P$2, C24.P$2, C25.P$2, C26.P$2, C27.P$2, C28.P$2, C29.P$2, C30.P$2, C31.P$2, C32.P$2, C33.P$2, C34.P$2, C35.P$2, C36.P$2, C37.P$2, D1.ANODE, J1.2, J2.2, R12.P$2, RA.1, RB.1, RC.1, SH1.2, SH2.2, SH3.2, SH4.1, U4.2 (PGND), U4.43 (BGND), U4.P1 (PAD), U4.P2 (PAD), U4.P3 (PAD), U4.P4 (PAD), U4.P5 (PAD), U4.P6 (PAD), U4.P7 (PAD), U4.P8 (PAD), U4.P9 (PAD), U4.P10 (PAD), U4.P11 (PAD), U4.P12 (PAD), U4.P13 (PAD), U4.P14 (PAD), U4.P15 (PAD), U4.P16 (PAD), U4.P17 (PAD), U4.P18 (PAD), U4.P19 (PAD), U4.P20 (PAD), U4.P21 (PAD), U4.P22 (PAD), U4.P23 (PAD), U4.P24 (PAD), U4.P25 (PAD), U4.PAD
VBAT_SENSE: R5.P$1, R6.P$2, U1.30 (PA8)
VTEMP_FET: C13.P$1, R8.P$2, R9.P$1, U1.31 (PA9)
VTEMP_MOT: R7.P$1, TEMP2.P$1, U1.25 (PB12)



Board: 4 copper layers, 46.0 x 53.0 mm, 105 parts (8 on the bottom side), 67 nets.

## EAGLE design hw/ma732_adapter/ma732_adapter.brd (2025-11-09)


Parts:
A: TSSOP_PAD
B: TSSOP_PAD
CLK: TSSOP_PAD
CSN: TSSOP_PAD
GND: TSSOP_PAD
MISO: TSSOP_PAD
MOSI: TSSOP_PAD
PWM: TSSOP_PAD
TEST: TSSOP_PAD
U: TSSOP_PAD
U$1: QFN16-BO; QFN16
V: TSSOP_PAD
VDD, VDD3V: TSSOP_PAD
W: TSSOP_PAD

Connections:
unnamed: CSN.P$1, U$1.5
unnamed: CLK.P$1, U$1.12
unnamed: MISO.P$1, U$1.7
unnamed: MOSI.P$1, U$1.4
unnamed: TEST.P$1, U$1.10
unnamed: B.P$1, U$1.6
unnamed: A.P$1, U$1.2
unnamed: PWM.P$1, U$1.9
unnamed: GND.P$1, U$1.8, U$1.EXP (PAD)
unnamed: U$1.13, VDD3V.P$1


Board: 2 copper layers, 6.3 x 6.3 mm, 15 parts (0 on the bottom side), 10 nets.

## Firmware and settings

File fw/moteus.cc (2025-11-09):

// Copyright 2023 mjbots Robotic Systems, LLC.  info@mjbots.com
//
// Licensed under the Apache License, Version 2.0 (the "License");
// you may not use this file except in compliance with the License.
// You may obtain a copy of the License at
//
//     http://www.apache.org/licenses/LICENSE-2.0
//
// Unless required by applicable law or agreed to in writing, software
// distributed under the License is distributed on an "AS IS" BASIS,
// WITHOUT WARRANTIES OR CONDITIONS OF ANY KIND, either express or implied.
// See the License for the specific language governing permissions and
// limitations under the License.

#include <inttypes.h>

#include <functional>

#include "mbed.h"

#include "mjlib/micro/async_exclusive.h"
#include "mjlib/micro/async_stream.h"
#include "mjlib/micro/command_manager.h"
#include "mjlib/micro/persistent_config.h"
#include "mjlib/micro/telemetry_manager.h"
#include "mjlib/multiplex/micro_server.h"
#include "mjlib/multiplex/micro_stream_datagram.h"

#include "fw/board_debug.h"
#include "fw/clock_manager.h"
#include "fw/firmware_info.h"
#include "fw/git_info.h"
#include "fw/millisecond_timer.h"
#include "fw/moteus_controller.h"
#include "fw/moteus_hw.h"
#include "fw/system_info.h"
#include "fw/uuid.h"

#if defined(TARGET_STM32G4)
#include "fw/fdcan.h"
#include "fw/fdcan_micro_server.h"
#include "fw/stm32g4_async_uart.h"
#include "fw/stm32g4_flash.h"
#else
#error "Unknown target"
#endif

extern "C" {
  uint32_t kMoteusFirmwareVersion = MOTEUS_FIRMWARE_VERSION;
}

auto* const MyDWT = DWT;
auto* const MyFLASH = FLASH;

using namespace moteus;
namespace micro = mjlib::micro;
namespace multiplex = mjlib::multiplex;

#if defined(TARGET_STM32G4)
using HardwareUart = Stm32G4AsyncUart;
using Stm32Flash = Stm32G4Flash;
#else
#error "Unknown target"
#endif

extern "C" {
void SetupClock() {
#if defined(TARGET_STM32G4)
  {
    __HAL_RCC_SYSCFG_CLK_ENABLE();
    __HAL_RCC_PWR_CLK_ENABLE();

    RCC_ClkInitTypeDef RCC_ClkInitStruct;

    RCC_ClkInitStruct.ClockType      = (RCC_CLOCKTYPE_SYSCLK | RCC_CLOCKTYPE_HCLK | RCC_CLOCKTYPE_PCLK1 | RCC_CLOCKTYPE_PCLK2);
    RCC_ClkInitStruct.SYSCLKSource = RCC_SYSCLKSOURCE_PLLCLK;
    RCC_ClkInitStruct.AHBCLKDivider = RCC_SYSCLK_DIV1; // 170 MHz
    RCC_ClkInitStruct.APB1CLKDivider = RCC_HCLK_DIV2;  //  85 MHz
    RCC_ClkInitStruct.APB2CLKDivider = RCC_HCLK_DIV2;  //  85 MHz

    if (HAL_RCC_ClockConfig(&RCC_ClkInitStruct, FLASH_LATENCY_6) != HAL_OK) {
      mbed_die();
    }

    RCC_PeriphCLKInitTypeDef PeriphClkInit = {};

    PeriphClkInit.PeriphClockSelection =
        RCC_PERIPHCLK_FDCAN |
        RCC_PERIPHCLK_USART2 |
        RCC_PERIPHCLK_USART3 |
        RCC_PERIPHCLK_ADC12 |
        RCC_PERIPHCLK_ADC345 |
        RCC_PERIPHCLK_I2C1
        ;
    PeriphClkInit.FdcanClockSelection = RCC_FDCANCLKSOURCE_PCLK1;
    PeriphClkInit.Usart2ClockSelection = RCC_USART2CLKSOURCE_PCLK1;
    PeriphClkInit.Usart3ClockSelection = RCC_USART3CLKSOURCE_PCLK1;
    PeriphClkInit.Adc12ClockSelection = RCC_ADC12CLKSOURCE_SYSCLK;
    PeriphClkInit.Adc345ClockSelection = RCC_ADC345CLKSOURCE_SYSCLK;
    PeriphClkInit.I2c1ClockSelection = RCC_I2C1CLKSOURCE_SYSCLK;
    if (HAL_RCCEx_PeriphCLKConfig(&PeriphClkInit) != HAL_OK) {
      mbed_die();
    }

    __HAL_RCC_TIM2_CLK_ENABLE();
    __HAL_RCC_TIM3_CLK_ENABLE();
    __HAL_RCC_TIM4_CLK_ENABLE();
  }
#endif
}
}

#if defined(TARGET_STM32G4)
extern "C" {
extern char _sccmram;
extern char _siccmram;
extern char _eccmram;
extern char _sccmram;
}
#endif

namespace moteus {
volatile uint8_t g_measured_hw_family;
volatile uint8_t g_measured_hw_rev;
volatile uint8_t g_measured_hw_pins;
MoteusHwPins g_hw_pins;
}

namespace {
struct CanConfig {
  uint32_t prefix = 0;

  template <typename Archive>
  void Serialize(Archive* a) {
    a->Visit(MJ_NVP(prefix));
  }

  bool operator==(const CanConfig& rhs) const {
    return prefix == rhs.prefix;
  }
};
}

int main(void) {
#if defined(TARGET_STM32G4)
  std::memcpy(&_sccmram, &_siccmram, &_eccmram - &_sccmram);
#endif

  FLASH->ACR |= FLASH_ACR_PRFTEN | FLASH_ACR_ICEN | FLASH_ACR_DCEN;

#if 0
  // We map SRAM1 onto address 0 just to make finding accesses to
  // address 0 easier.
  SYSCFG->MEMRMP = (SYSCFG->MEMRMP & ~SYSCFG_MEMRMP_MEM_MODE_Msk) | 0x03;  // SRAM1
#endif

  SetupClock();

  // I initially used a Ticker here to enqueue events at 1ms
  // intervals.  However, it introduced jitter into the current
  // sampling interrupt, and I couldn't figure out how to get the
  // interrupt priorities right.  Thus for now we just poll to look
  // for millisecond turnover.
  MillisecondTimer timer;

  const auto family_and_version = DetectMoteusFamily(&timer);
  g_measured_hw_family = family_and_version.family;
  g_measured_hw_rev = family_and_version.hw_version;
  g_measured_hw_pins = family_and_version.hw_pins;

  g_hw_pins = FindHardwarePins(family_and_version);

  // We do our compatibility check *after* calling FindHardwarePins so
  // the the family specific pins are known.  That way mbed_die
  // doesn't choke being unable to find the power LED for instance.

  if (family_and_version.hw_version < 0) {
    // This firmware is not compatible with this board.
    mbed_die();
  }

  // We require cycle counting be enabled for some things.
  {
    ITM->LAR = 0xC5ACCE55;
    CoreDebug->DEMCR |= CoreDebug_DEMCR_TRCENA_Msk;
    DWT->CYCCNT = 0;
    DWT->CTRL |= DWT_CTRL_CYCCNTENA_Msk;
  }

  // Turn on our power light.
  DigitalOut power_led(g_hw_pins.power_led, 0);

  micro::SizedPool<20000> pool;

  std::optional<HardwareUart> rs485;
  if (g_hw_pins.uart_tx != NC) {
    rs485.emplace(&pool, &timer, []() {
      HardwareUart::Options options;
      options.tx = g_hw_pins.uart_tx;
      options.rx = g_hw_pins.uart_rx;
      options.dir = g_hw_pins.uart_dir;
      options.baud_rate = 3000000;
      return options;
                                 }());
  }

  FDCan fdcan([]() {
      FDCan::Options options;

      options.td = g_hw_pins.can_td;
      options.rd = g_hw_pins.can_rd;

      options.slow_bitrate = 1000000;
      options.fast_bitrate = 5000000;

      options.fdcan_frame = true;
      options.bitrate_switch = true;
      options.automatic_retransmission = true;

      // Family 0 uses a TCAN334GDCNT, which has a very low loop
      // delay.  Other families use chips with a longer loop delay.
      options.delay_compensation = g_measured_hw_family != 0;

      options.tdc_offset = 13;  // 13 / 85MHz ~= 152ns
      options.tdc_filter = 2; // 2 / 85MHz ~= 23ns

      return options;
    }());
  FDCanMicroServer fdcan_micro_server(&fdcan);
  multiplex::MicroServer multiplex_protocol(
      &pool, &fdcan_micro_server,
      []() {
        multiplex::MicroServer::Options options;
        options.max_tunnel_streams = 3;
        return options;
      }());

  micro::AsyncStream* serial = multiplex_protocol.MakeTunnel(1);

  micro::AsyncExclusive<micro::AsyncWriteStream> write_stream(serial);
  micro::CommandManager command_manager(&pool, serial, &write_stream);
  char micro_output_buffer[2048] = {};
  micro::TelemetryManager telemetry_manager(
      &pool, &command_manager, &write_stream, micro_output_buffer);
  Stm32Flash flash_interface;
  micro::PersistentConfig persistent_config(
      pool, command_manager, flash_interface, micro_output_buffer);

  SystemInfo system_info(pool, telemetry_manager);
  FirmwareInfo firmware_info(pool, telemetry_manager,
                             kMoteusFirmwareVersion, MOTEUS_MODEL_NUMBER);
  Uuid uuid(persistent_config);
  ClockManager clock(&timer, persistent_config, command_manager);

  MoteusController moteus_controller(
      &pool, &persistent_config,
      &command_manager,
      &telemetry_manager,
      &multiplex_protocol,
      &clock,
      &system_info,
      &timer,
      &firmware_info,
      &uuid);

  BoardDebug board_debug(
      &pool, &command_manager, &telemetry_manager, &multiplex_protocol,
      moteus_controller.bldc_servo());

  GitInfo git_info;
  telemetry_manager.Register("git", &git_info);

  CanConfig can_config, old_can_config;

  // We always want to update our filters at least once.
  uint8_t old_multiplex_id = 255;

  const auto maybe_update_filters =
      [&can_config, &fdcan, &fdcan_micro_server, &old_can_config,
       &old_multiplex_id, &multiplex_protocol]() {
        // We only update our config if it has actually changed.
        // Re-initializing the CAN-FD controller can cause packets to
        // be lost, so don't do it unless actually necessary.
        if (can_config == old_can_config &&
            multiplex_protocol.config()->id == old_multiplex_id) {
          return;
        }
        old_can_config = can_config;
        old_multiplex_id = multiplex_protocol.config()->id;

        FDCan::Filter filters[4] = {};
        filters[0].id1 = (can_config.prefix << 16) | old_multiplex_id;
        filters[0].id2 = 0x1fff00ffu;
        filters[0].mode = FDCan::FilterMode::kMask;
        filters[0].action = FDCan::FilterAction::kAccept;
        filters[0].type = FDCan::FilterType::kExtended;

        filters[1].id1 = (can_config.prefix << 16) | 0x7f;
        filters[1].id2 = 0x1fff00ffu;
        filters[1].mode = FDCan::FilterMode::kMask;
        filters[1].action = FDCan::FilterAction::kAccept;
        filters[1].type = FDCan::FilterType::kExtended;

        filters[2].id1 = (can_config.prefix << 16) | old_multiplex_id;
        filters[2].id2 = 0x1fff00ffu;
        filters[2].mode = FDCan::FilterMode::kMask;
        filters[2].action = FDCan::FilterAction::kAccept;
        filters[2].type = FDCan::FilterType::kStandard;

        filters[3].id1 = (can_config.prefix << 16) | 0x7f;
        filters[3].id2 = 0x1fff00ffu;
        filters[3].mode = FDCan::FilterMode::kMask;
        filters[3].action = FDCan::FilterAction::kAccept;
        filters[3].type = FDCan::FilterType::kStandard;

        FDCan::FilterConfig filter_config;
        filter_config.begin = std::begin(filters);
        filter_config.end = std::end(filters);
        filter_config.global_std_action = FDCan::FilterAction::kReject;
        filter_config.global_ext_action = FDCan::FilterAction::kReject;
        fdcan.ConfigureFilters(filter_config);

        fdcan_micro_server.SetPrefix(can_config.prefix);
      };

  persistent_config.Register("id", multiplex_protocol.config(), maybe_update_filters);

  persistent_config.Register("can", &can_config, maybe_update_filters);

  persistent_config.Load();

  moteus_controller.Start();
  command_manager.AsyncStart();
  multiplex_protocol.Start(moteus_controller.multiplex_server());

  auto old_time = timer.read_us();

  for (;;) {
    if (rs485) {
      rs485->Poll();
    }
#if defined(TARGET_STM32G4)
    fdcan_micro_server.Poll();
#endif
    moteus_controller.Poll();
    multiplex_protocol.Poll();

    const auto new_time = timer.read_us();

    const auto delta_us = MillisecondTimer::subtract_us(new_time, old_time);
    if (moteus_controller.bldc_servo()->config().timing_fault &&
        delta_us >= 4000) {
      // We missed several entire polling cycles.  Fault if we can.
      moteus_controller.bldc_servo()->Fault(moteus::errc::kTimingViolation);
    }

    if (delta_us >= 1000) {
      telemetry_manager.PollMillisecond();
      system_info.PollMillisecond();
      moteus_controller.PollMillisecond();
      board_debug.PollMillisecond();
      system_info.SetCanResetCount(fdcan_micro_server.can_reset_count());
      timer.AdvanceMsSinceBoot();

      old_time += 1000;
    }

    SystemInfo::idle_count++;
  }

  return 0;
}

extern "C" {
  void abort() {
    mbed_die();
  }
}

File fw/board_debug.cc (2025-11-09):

// Copyright 2023 mjbots Robotic Systems, LLC.  info@mjbots.com
//
// Licensed under the Apache License, Version 2.0 (the "License");
// you may not use this file except in compliance with the License.
// You may obtain a copy of the License at
//
//     http://www.apache.org/licenses/LICENSE-2.0
//
// Unless required by applicable law or agreed to in writing, software
// distributed under the License is distributed on an "AS IS" BASIS,
// WITHOUT WARRANTIES OR CONDITIONS OF ANY KIND, either express or implied.
// See the License for the specific language governing permissions and
// limitations under the License.

#include "fw/board_debug.h"

#include <cctype>
#include <cstdlib>
#include <functional>
#include <numeric>

#include "mbed.h"

#include "mjlib/base/inplace_function.h"
#include "mjlib/base/tokenizer.h"
#include "mjlib/base/visitor.h"

#include "fw/as5047.h"
#include "fw/bldc_servo.h"
#include "fw/bootloader.h"
#include "fw/drv8323.h"
#include "fw/moteus_hw.h"
#include "fw/strtof.h"

namespace base = mjlib::base;
namespace micro = mjlib::micro;
namespace multiplex = mjlib::multiplex;

namespace moteus {
constexpr float kCalibrationStep = 0.002;
constexpr float kMaxCalPoleCount = 50.0f;

namespace {
void recurse(int count, base::inplace_function<void(int)> callback) {
  callback(count - 1);
}

bool ParseOptions(BldcServo::CommandData* command, base::Tokenizer* tokenizer,
                  const char* valid_options) {
  while (tokenizer->remaining().size()) {
    const auto token = tokenizer->next();
    // We accept optional arguments, each prefixed by a single
    // character.
    if (token.size() < 1) { continue; }
    const char option = token[0];
    if (::strchr(valid_options, option) == nullptr) {
      return false;
    }

    const auto maybe_value = Strtof(&token[1]);
    if (!maybe_value) {
      return false;
    }
    const auto value = *maybe_value;
    switch (option) {
      case 'p': {
        command->kp_scale = value;
        break;
      }
      case 'd': {
        command->kd_scale = value;
        break;
      }
      case 'i': {
        command->ilimit_scale = value;
        break;
      }
      case 's': {
        command->stop_position = value;
        break;
      }
      case 'f': {
        command->feedforward_Nm = value;
        break;
      }
      case 't': {
        command->timeout_s = value;
        break;
      }
      case 'a': {
        command->accel_limit = value;
        break;
      }
      case 'v': {
        command->velocity_limit = value;
        break;
      }
      case 'o': {
        command->fixed_voltage_override = value;
        break;
      }
      case 'c': {
        command->fixed_current_override = value;
        break;
      }
      case 'b': {
        command->ignore_position_bounds = value != 0.0f;
        break;
      }
      default: {
        return false;
      }
    }
  }
  return true;
}
}

class BoardDebug::Impl {
 public:
  struct HistogramSource;

  Impl(micro::Pool* pool,
       micro::CommandManager* command_manager,
       micro::TelemetryManager* telemetry_manager,
       multiplex::MicroServer* multiplex_protocol,
       BldcServo* bldc_servo)
      : multiplex_protocol_(multiplex_protocol),
        bldc_(bldc_servo) {
    command_manager->Register(
        "d", std::bind(&Impl::HandleCommand, this,
                       std::placeholders::_1, std::placeholders::_2));

    data_update_ = telemetry_manager->Register("board_debug", &data_);
  }

  void PollMillisecond() {
    if (motor_cal_mode_ != kNoMotorCal) {
      DoCalibration();
    }
    if (histogram_active_) {
      DoHistogram();
    }
  }

  bool ParseHistogramChannel(HistogramSource* source, const std::string_view& spec) {
    // The format of this specification is a single character source:
    //
    //  t - electrical theta
    //  c - compensated
    //  f - filtered
    //  o - offset
    //  r - raw
    //  v - pll output velocity
    //  ... etc ...
    //
    // followed by an optional single digit to specify the encoder
    // channel, and then an optional list of non-digit flags:
    //
    //  d - derivative

    source->derivative = false;
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

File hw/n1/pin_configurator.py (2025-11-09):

#!/usr/bin/python3

# Copyright 2023 mjbots Robotic Systems, LLC.  info@mjbots.com
#
# Licensed under the Apache License, Version 2.0 (the "License");
# you may not use this file except in compliance with the License.
# You may obtain a copy of the License at
#
#     http://www.apache.org/licenses/LICENSE-2.0
#
# Unless required by applicable law or agreed to in writing, software
# distributed under the License is distributed on an "AS IS" BASIS,
# WITHOUT WARRANTIES OR CONDITIONS OF ANY KIND, either express or implied.
# See the License for the specific language governing permissions and
# limitations under the License.

import argparse
import enum
import re
import sys


class MatchStatus(enum.IntEnum):
    VALID = 1
    INCONCLUSIVE = 0
    IMPOSSIBLE = -1


def generic_search(data, to_find):
    found = [d.find(to_find) >= 0 for d in data]
    if any(found):
        return found.index(True)
    return None

def find_and_remove(data, to_find, compare=generic_search):
    hit = compare(data, to_find)
    if hit is not None:
        del(data[hit])
        return 1
    return 0


class Desired5V:
    def __init__(self, args):
        self.args = args

    def __call__(self, pins):
        for pin in pins:
            for subpin in pin.split('/'):
                if subpin.find('5V') < 0:
                    return MatchStatus.IMPOSSIBLE
        if len(pins) == self.args.pins:
            return MatchStatus.VALID
        return MatchStatus.INCONCLUSIVE


class DesiredADC:
    def __init__(self, args):
        self.args = args
        self.available_adcs = [
            x for x in ['ADC1', 'ADC2', 'ADC3', 'ADC4']
            if x not in self.args.exclude
        ]

    def all_analog(self, maybe_pair):
        pins = maybe_pair.split('/')
        return all([x.find('ANALOG') >= 0 for x in pins])

    def find_adc(self, data, to_find):
        found = [d.find(to_find) >= 0 and self.all_analog(d) for d in data]
        if any(found):
            return found.index(True)
        return None

    def __call__(self, pins):
        # This is not strictly correct, as it will count multiple
        # channels on the same pin as multiple ADCs.  We'll fix that
        # in an ad-hoc way if it matters.

        adc_present = []
        pins_copy = pins[:]
        for adc in self.available_adcs:
            adc_present.append(find_and_remove(pins_copy, adc,
                                               compare=self.find_adc))

        count = sum(adc_present)
        if count == 2:
            return MatchStatus.VALID
        elif (2 - count) + len(pins) > self.args.pins:
            return MatchStatus.IMPOSSIBLE
        else:
            return MatchStatus.INCONCLUSIVE


class DesiredUART:
    def __init__(self, args):
        self.args = args
        self.available_uarts = [
            x for x in ['USART1', 'USART2', 'USART3', 'UART4', 'UART5', 'LPUART1']
            if x not in self.args.exclude
        ]

    def __call__(self, pins):

        results = []
        for uart in self.available_uarts:
            pins_copy = pins[:]
            tx = find_and_remove(pins_copy, f'{uart}_TX')
            rx = find_and_remove(pins_copy, f'{uart}_RX')

            if tx > 0 and rx > 0:
                return MatchStatus.VALID
            elif (2 - tx - rx) + len(pins) > self.args.pins:
                results.append(MatchStatus.IMPOSSIBLE)
            else:
                results.append(MatchStatus.INCONCLUSIVE)
        return max(results)


class DesiredI2C:
    def __init__(self, args):
        self.args = args
        self.available_i2c = [
            x for x in ['I2C1', 'I2C2', 'I2C3', 'I2C4', 'I2C5']
            if x not in self.args.exclude
        ]

    def __call__(self, pins):
        results = []
        for i2c in self.available_i2c:
            pins_copy = pins[:]
            sda = find_and_remove(pins_copy, f'{i2c}_SDA')
            scl = find_and_remove(pins_copy, f'{i2c}_SCL')

            if sda > 0 and scl > 0:
                return MatchStatus.VALID
            elif (2 - sda - scl) + len(pins) > self.args.pins:
                results.append(MatchStatus.IMPOSSIBLE)
            else:
                results.append(MatchStatus.INCONCLUSIVE)

        return max(results)


class DesiredQuadrature:
    def __init__(self, args):
        self.args = args
        self.available_timers = [
            x for x in ['TIM1', 'TIM2', 'TIM3', 'TIM4', 'TIM5', 'TIM8', 'TIM20']
            if x not in self.args.exclude
        ]

    def __call__(self, pins):
        results = []

        for timer in self.available_timers:
            pins_copy = pins[:]
            ch1 = find_and_remove(pins_copy, f'{timer}_CH1')
            ch2 = find_and_remove(pins_copy, f'{timer}_CH2')

            if ch1 > 0 and ch2 > 0:
                return MatchStatus.VALID
            elif (2 - ch1 - ch1) + len(pins) > self.args.pins:
                results.append(MatchStatus.IMPOSSIBLE)
            else:
                results.append(MatchStatus.INCONCLUSIVE)
        return max(results)


class DesiredSpi:
    def __init__(self, args):
        self.args = args
        self.available_spi = [
            x for x in ['SPI1', 'SPI2', 'SPI3', 'SPI4', 'SPI5']
            if x not in self.args.exclude
        ]

    def any_non_five_volt(self, pins_copy):
        for pin_pair in pins_copy:
            for pin in pin_pair.split('/'):
                if pin.find('5V') < 0:
                    return True
        return False

    def __call__(self, pins):
        results = []

        # Just check all 5 SPI types.
        for spi in self.available_spi:
            sck = 0
            miso = 0
            mosi = 0

            pins_copy = pins[:]

            sck = find_and_remove(pins_copy, f'{spi}_SCK')
            miso = find_and_remove(pins_copy, f'{spi}_MISO')
            mosi = find_and_remove(pins_copy, f'{spi}_MOSI')

            if self.args.nonspi_five_volt:
                # All remaining pins must be 5V.
                if self.any_non_five_volt(pins_copy):
                    results.append(MatchStatus.IMPOSSIBLE)
                    continue


            if sck > 0 and miso > 0 and mosi > 0:
                return MatchStatus.VALID
            elif (3 - sck - miso - mosi) + len(pins) > self.args.pins:
                results.append(MatchStatus.IMPOSSIBLE)
            else:
                results.append(MatchStatus.INCONCLUSIVE)
        return max(results)

    def find_nonspi(self, pins):
        results = []

        # Just check all 5 SPI types.
        for spi in self.available_spi:
            sck = 0
            miso = 0
            mosi = 0

            pins_copy = pins[:]

            sck = find_and_remove(pins_copy, f'{spi}_SCK')
            miso = find_and_remove(pins_copy, f'{spi}_MISO')
            mosi = find_and_remove(pins_copy, f'{spi}_MOSI')

            if sck > 0 and miso > 0 and mosi > 0:
                return pins_copy
        return None
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

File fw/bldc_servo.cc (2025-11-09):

// Copyright 2023 mjbots Robotic Systems, LLC.  info@mjbots.com
//
// Licensed under the Apache License, Version 2.0 (the "License");
// you may not use this file except in compliance with the License.
// You may obtain a copy of the License at
//
//     http://www.apache.org/licenses/LICENSE-2.0
//
// Unless required by applicable law or agreed to in writing, software
// distributed under the License is distributed on an "AS IS" BASIS,
// WITHOUT WARRANTIES OR CONDITIONS OF ANY KIND, either express or implied.
// See the License for the specific language governing permissions and
// limitations under the License.

#include "bldc_servo.h"

#include <atomic>
#include <cmath>
#include <functional>

#include "mbed.h"

#include "PeripheralPins.h"

#include "mjlib/base/assert.h"
#include "mjlib/base/windowed_average.h"

#include "fw/bldc_servo_position.h"
#include "fw/foc.h"
#include "fw/math.h"
#include "fw/moteus_hw.h"
#include "fw/stm32g4_adc.h"
#include "fw/thermistor.h"
#include "fw/torque_model.h"

#if defined(TARGET_STM32G4)
#include "fw/stm32g4_async_uart.h"
#else
#error "Unknown target"
#endif

#ifdef wait_us
#undef wait_us
#endif

namespace micro = mjlib::micro;

namespace moteus {

namespace {
#if defined(TARGET_STM32G4)
using HardwareUart = Stm32G4AsyncUart;
#else
#error "Unknown target"
#endif


float Limit(float, float, float) MOTEUS_CCM_ATTRIBUTE;

float Limit(float a, float min, float max) {
  if (a < min) { return min; }
  if (a > max) { return max; }
  return a;
}

// This variant, in addition to performing the limiting, will return
// the `code_limit` if limiting was performed and `code_nolimit` if no
// limiting was performed.  It can be used to chain operations, to
// determine which operation caused any limiting to occur.
std::pair<float, errc> LimitCode(float, float, float, errc, errc) MOTEUS_CCM_ATTRIBUTE;

std::pair<float, errc> LimitCode(float a, float min, float max, errc code_limit, errc code_nolimit) {
  if (a < min) { return {min, code_limit}; }
  if (a > max) { return {max, code_limit}; }
  return {a, code_nolimit};
}

float Threshold(float, float, float) MOTEUS_CCM_ATTRIBUTE;

float Threshold(float value, float lower, float upper) {
  if (value > lower && value < upper) { return 0.0f; }
  return value;
}

float Interpolate(float, float, float, float, float) MOTEUS_CCM_ATTRIBUTE;

float Interpolate(float x, float xl, float xh, float vl, float vh) {
  return (x - xl) / (xh - xl) * (vh - vl) + vl;
}

template <typename Array>
int MapConfig(const Array& array, int value) {
  static_assert(sizeof(array) > 0);
  int result = 0;
  for (const auto& item : array) {
    if (value <= item) { return result; }
    result++;
  }
  // Never return past the end.
  return result - 1;
}

// This is used to determine the maximum allowable PWM value so that
// the current sampling is guaranteed to occur while the FETs are
// still low.  It was calibrated using the scope and trial and error.
//
// The primary test is a high torque pulse with absolute position
// limits in place of +-1.0.  Something like "d pos nan 0 1 p0 d0 f1".
// This all but ensures the current controller will saturate.
//
// As of 2020-09-13, 0.98 was the highest value that failed.
constexpr float kCurrentSampleTime = 1.03e-6f;


// All of these constants depend upon the pwm rate.
struct RateConfig {
  int int_rate_hz;
  int interrupt_divisor;
  uint32_t interrupt_mask;
  int pwm_rate_hz;
  float min_pwm;
  float max_pwm;
  float max_voltage_ratio;
  float rate_hz;
  float period_s;
  int16_t max_position_delta;

  RateConfig(int pwm_rate_hz_in = 30000) {
    const int board_min_pwm_rate_hz =
        (g_measured_hw_family == 0 &&
         g_measured_hw_rev == 2) ? 60000 :
        15000;

    // Limit our PWM rate to even frequencies between 15kHz and 60kHz.
    pwm_rate_hz =
        ((std::max(board_min_pwm_rate_hz,
                   std::min(60000, pwm_rate_hz_in))) / 2) * 2;

    interrupt_divisor = (pwm_rate_hz > 30000) ? 2 : 1;
    interrupt_mask = [&]() {
                       switch (interrupt_divisor) {
                         case 1: return 0;
                         case 2: return 1;
                         default: mbed_die();
                       }
                     }();

    // The maximum interrupt rate is 30kHz, so if our PWM rate is
    // higher than that, then set up the interrupt at half rate.
    int_rate_hz = pwm_rate_hz / interrupt_divisor;

    min_pwm = kCurrentSampleTime / (0.5f / static_cast<float>(pwm_rate_hz));
    max_pwm = 1.0f - min_pwm;
    max_voltage_ratio = ((max_pwm - 0.5f) * 2.0f);

    rate_hz = int_rate_hz;
    period_s = 1.0f / rate_hz;

    // The maximum amount the absolute encoder can change in one cycle
    // without triggering a fault.  Measured as a fraction of a uint16_t
    // and corresponds to roughly 28krpm, which is the limit of the AS5047
    // encoder.
    //  28000 / 60 = 467 Hz
    //  467 Hz * 65536 / kIntRate ~= 763
    max_position_delta = 28000 / 60 * 65536 / int_rate_hz;
  }
};

constexpr int kCalibrateCount = 256;

constexpr float kDefaultTorqueConstant = 0.1f;
constexpr float kMaxUnconfiguredCurrent = 5.0f;

constexpr int kMaxVelocityFilter = 256;

IRQn_Type FindUpdateIrq(TIM_TypeDef* timer) {
#if defined(TARGET_STM32G4)
  if (timer == TIM2) {
    return TIM2_IRQn;
  } else if (timer == TIM3) {
    return TIM3_IRQn;
  } else if (timer == TIM4) {
    return TIM4_IRQn;
  } else if (timer == TIM5) {
    return TIM5_IRQn;
  }
  MJ_ASSERT(false);
  return TIM2_IRQn;
#else
#error "Unknown target"
#endif
}

volatile uint32_t* FindCcr(TIM_TypeDef* timer, PinName pin) {
  const auto function = pinmap_function(pin, PinMap_PWM);

  const auto inverted = STM_PIN_INVERTED(function);
  MJ_ASSERT(!inverted);

  const auto channel = STM_PIN_CHANNEL(function);

  switch (channel) {
    case 1: { return &timer->CCR1; }
    case 2: { return &timer->CCR2; }
    case 3: { return &timer->CCR3; }
    case 4: { return &timer->CCR4; }
  }
  MJ_ASSERT(false);
  return nullptr;
}

uint32_t FindSqr(PinName pin) {
  const auto function = pinmap_function(pin, PinMap_ADC);

  const auto channel = STM_PIN_CHANNEL(function);
  return channel;
}
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

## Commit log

2025-11-09 Fix another typo in the new docs
    [20230523-moteus-n1-r1_3-mechanical.step, aux1.kicad_sch, aux2-hall-sample.kicad_pcb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]
2026-05-05 Add comprehensive system flowchart for MPC+Kalman+SMO+RLS integration

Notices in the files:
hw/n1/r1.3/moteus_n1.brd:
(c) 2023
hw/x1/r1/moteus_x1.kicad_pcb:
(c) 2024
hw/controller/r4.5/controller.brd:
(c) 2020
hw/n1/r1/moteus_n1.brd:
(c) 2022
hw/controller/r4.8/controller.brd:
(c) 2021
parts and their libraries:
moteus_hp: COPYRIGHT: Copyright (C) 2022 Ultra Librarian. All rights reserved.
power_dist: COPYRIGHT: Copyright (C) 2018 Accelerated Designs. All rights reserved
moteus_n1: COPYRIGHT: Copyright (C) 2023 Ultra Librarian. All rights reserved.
